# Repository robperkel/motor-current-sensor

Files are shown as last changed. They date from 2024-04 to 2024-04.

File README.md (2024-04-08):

# Hall Effect Current Sensor

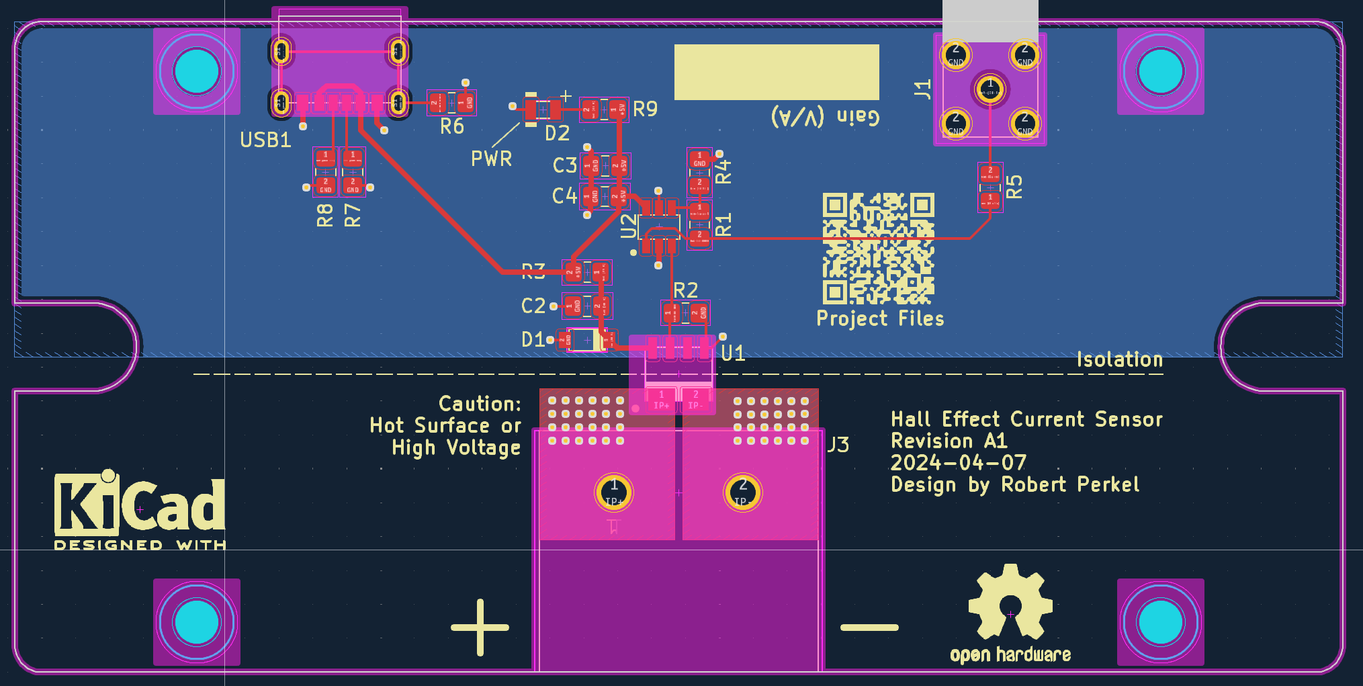
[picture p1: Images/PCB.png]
PCB Screenshot
  

## Disclaimer

**Build and use this circuit at your own risk.** This circuit has not been tested to determine the maximum current possible (without the PCB igniting/melting) or the maximum input voltage on the current sensing side.

If high voltages are applied to the current sense side, the PCB may become a shock hazard. While the current sense side is isolated from the outputs - arcing, debris/dirt, assembly errors or design defects could cause it to jump to the output side. **Excerise extreme caution when working with hazardous voltages.**

## Tools and Components

- [KiCad 8.0.1](https://www.kicad.org/)  
- [FreeCad](https://www.freecad.org/)  

## Measuring the Current

The objective of this circuit is to measure current in an isolated fashion. For me (the author), this is to characterize current flow in a Stepper Motor, however this design can be used in other applications. To perform this task, a [Hall Effect sensor (ACS37030) by Allegro Microsystems](https://www.allegromicro.com/en/products/sense/current-sensor-ics/zero-to-fifty-amp-integrated-conductor-sensor-ics/acs37030-2) is used. 

**Note**: The ACS37030 has multiple different current ranges available, but at the time of this readme, only the 40A part is available. 

**Caution: While the sensor can measure high currents (20A/40A/65A), the PCB is NOT tested or characterized for this.** Use of high copper weight PCB material is likely required.  

This part was choosen due to it's high BW range (DC to 5 MHz), which is uncommon for these ICs. Since the current-side circuit is isolated, it is possible to measure current with high common voltages on the current sense side.

## Driving the Cable

To drive the cable to the oscilloscope, an [MCP633 Operational Amplifier by Microchip](https://www.microchip.com/en-us/product/MCP633) is implemented as a non-inverting amplifier with a gain of 3. The MCP633 has a Gain Bandwidth Product (GBWP) of 24 MHz, which provides enough BW to run at a gain of 3 without limiting the circuit performance. In this configuration, the output of this circuit is 99 mV/A. 

**Note**: The gain of the circuit can be changed by modifying the ratio of R1/R4 in the schematic. 

Power for this board is supplied over USB-C (at 5V). The ACS37030 is designed for 3V operation, so a simple Zener shunt regulator is used to regulate the power supply for the sensor, while the operational amplifier uses the raw USB bus voltage.

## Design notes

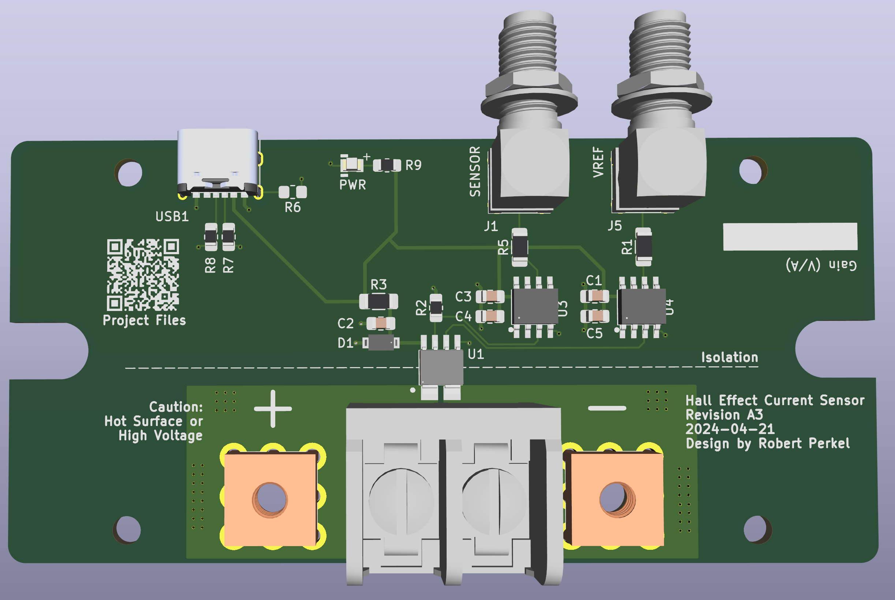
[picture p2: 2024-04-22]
Images/3D PCB Render.png

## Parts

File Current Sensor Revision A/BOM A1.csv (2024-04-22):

Reference | Value | Footprint | Qty | DNP
C1,C2,C3 | 0.1uF | Capacitor_SMD:C_0805_2012Metric_Pad1.18x1.45mm_HandSolder | 3
C4 | 10uF | Capacitor_SMD:C_0805_2012Metric_Pad1.18x1.45mm_HandSolder | 1
C5 | 10uF | Capacitor_SMD:C_0805_2012Metric_Pad1.18x1.45mm_HandSolder | 1 | DNP
D1 | MMSZ4684T1G | StandardPackages_Custom:SOT-123 | 1
D2 | LED | StandardPackages_Custom:LED 0805 | 1
J1,J5 | SMA | Current Sensor PCB Library:CONSMA002-L-G | 2
J2,J4 | 74650094R | Current Sensor PCB Library:74650094R | 2
J3 | Screw_Terminal_01x02 | Current Sensor PCB Library:6PCV-02-007 | 1
R1,R3,R5 | 50 | Resistor_SMD:R_1206_3216Metric_Pad1.30x1.75mm_HandSolder | 3
R2 | 100k | Resistor_SMD:R_0805_2012Metric_Pad1.20x1.40mm_HandSolder | 1
R6 | 0 | Resistor_SMD:R_0805_2012Metric_Pad1.20x1.40mm_HandSolder | 1 | DNP
R7,R8 | 5.1k | Resistor_SMD:R_0805_2012Metric_Pad1.20x1.40mm_HandSolder | 2
R9 | 1.8k | Resistor_SMD:R_0805_2012Metric_Pad1.20x1.40mm_HandSolder | 1
U1 | ACS37030 | Current Sensor PCB Library:Custom 6-pin SOIC (only for ACS37030ACS37032) | 1
U3,U4 | MCP631 | StandardPackages_Custom:SOIC-8 | 2
USB1 | USB_C_Receptacle_PowerOnly_6P | Current Sensor PCB Library:10164359-00011LF | 1

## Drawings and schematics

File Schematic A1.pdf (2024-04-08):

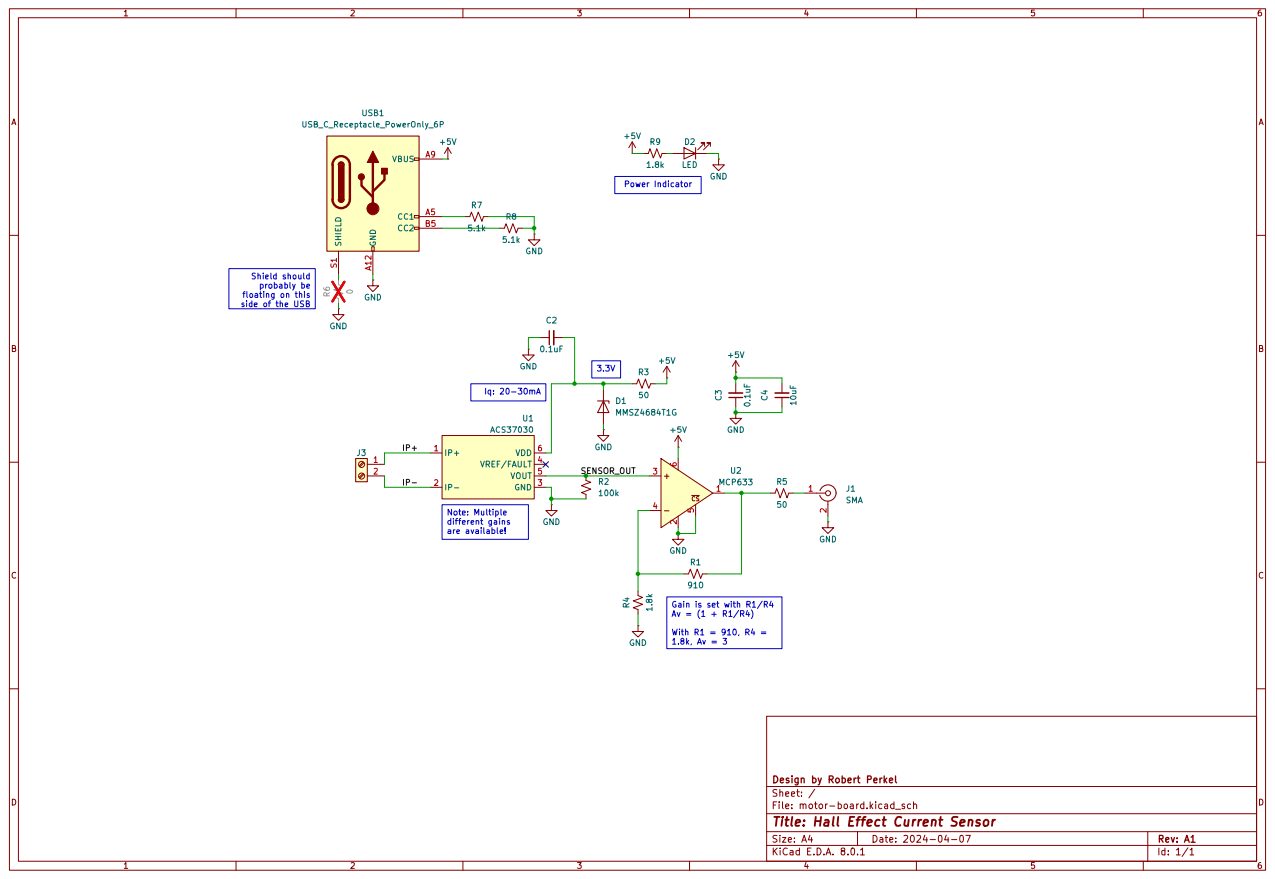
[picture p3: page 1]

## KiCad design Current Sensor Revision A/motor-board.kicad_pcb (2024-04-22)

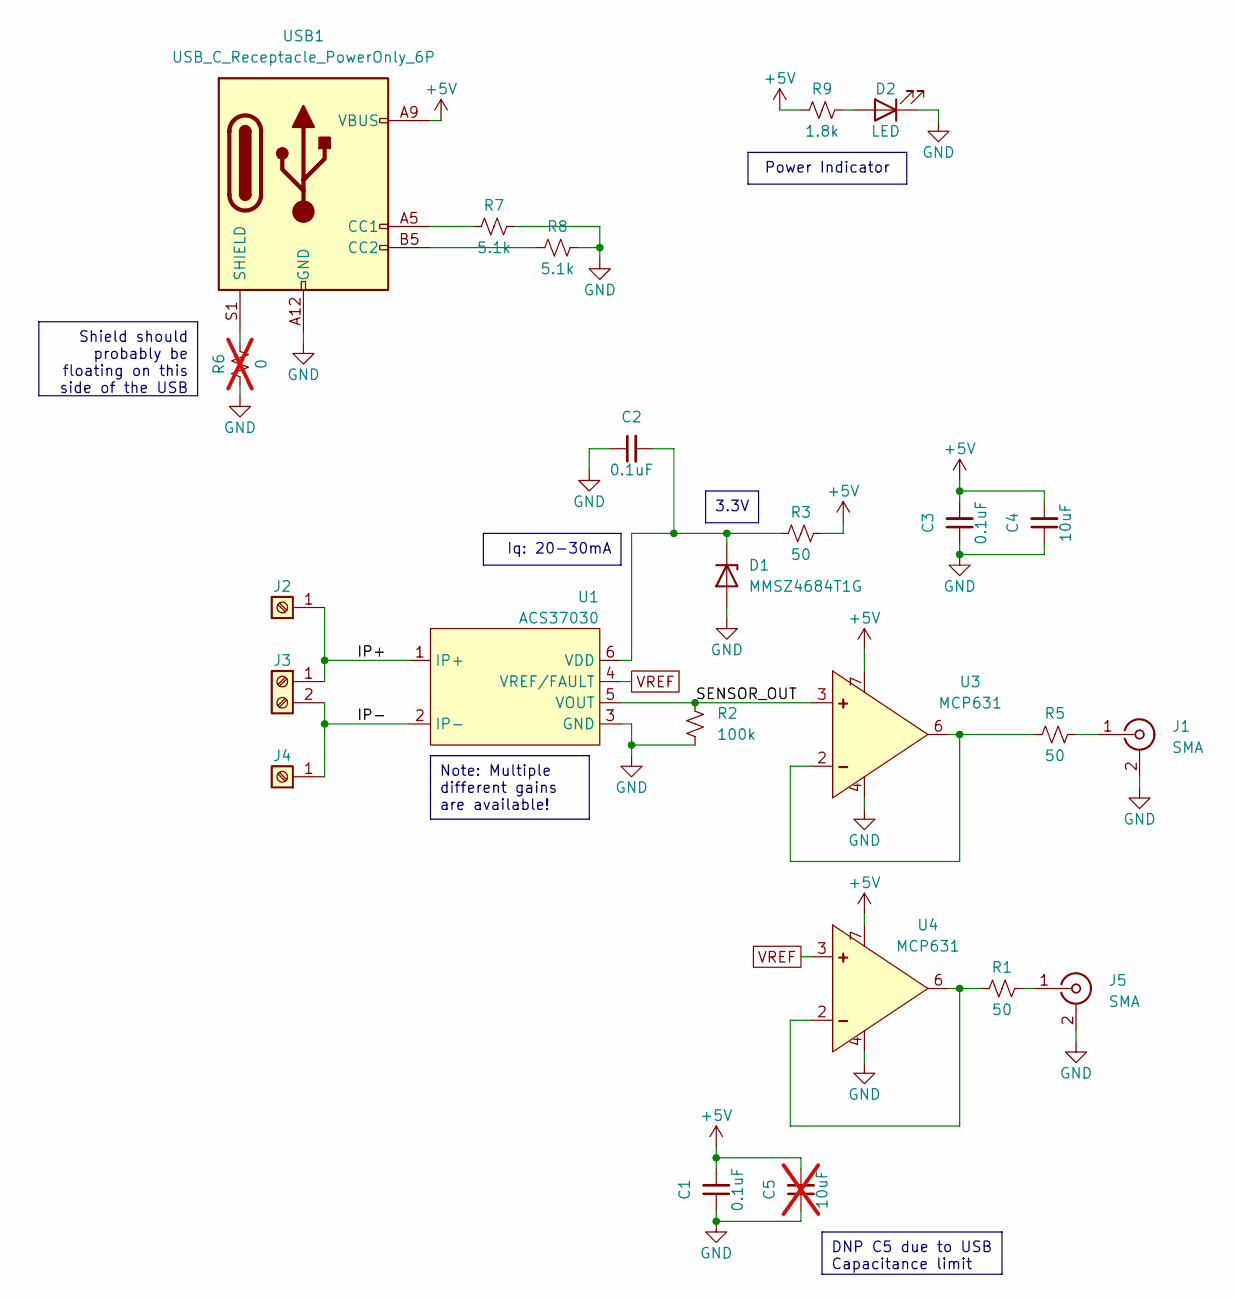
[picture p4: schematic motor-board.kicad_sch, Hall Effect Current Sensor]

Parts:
C1, C2, C3: 0.1uF; C_0805_2012Metric_Pad1.18x1.45mm_HandSolder
C4: 10uF; C_0805_2012Metric_Pad1.18x1.45mm_HandSolder
C5: 10uF; C_0805_2012Metric_Pad1.18x1.45mm_HandSolder; not fitted
D1: MMSZ4684T1G; SOT-123
D2: LED; LED 0805
J1, J5: SMA; CONSMA002-L-G
J2, J4: 74650094R
J3: Screw_Terminal_01x02; 6PCV-02-007
R1, R3, R5: 50; R_1206_3216Metric_Pad1.30x1.75mm_HandSolder
R2: 100k; R_0805_2012Metric_Pad1.20x1.40mm_HandSolder
R6: 0; R_0805_2012Metric_Pad1.20x1.40mm_HandSolder; not fitted
R7, R8: 5.1k; R_0805_2012Metric_Pad1.20x1.40mm_HandSolder
R9: 1.8k; R_0805_2012Metric_Pad1.20x1.40mm_HandSolder
U1: ACS37030; Custom 6-pin SOIC (only for ACS37030ACS37032)
U3, U4: MCP631; SOIC-8
USB1: USB_C_Receptacle_PowerOnly_6P; 10164359-00011LF

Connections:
+5V: C1.2, C3.2, C4.2, C5.2, R3.2, R9.1, U3.7 (VDD), U4.7 (VDD), USB1.A9 (VBUS), USB1.B9 (VBUS)
/IP+: J2.1, J3.1, U1.1 (IP+)
/IP-: J3.2, J4.1, U1.2 (IP-)
/SENSOR_OUT: R2.1, U1.5 (VOUT), U3.3 (IN+)
GND: C1.1, C2.1, C3.1, C4.1, C5.1, D1.2 (A), D2.1 (K), J1.2 (Ext), J5.2 (Ext), R2.2, R6.1, R7.2, R8.2, U1.3 (GND), U3.4 (VSS), U4.4 (VSS), USB1.A12 (GND), USB1.B12 (GND)
unnamed: C2.2, D1.1 (K), R3.1, U1.6 (VDD)
unnamed: D2.2 (A), R9.2
unnamed: J1.1 (In), R5.2
unnamed: J5.1 (In), R1.2
unnamed: R5.1, U3.2 (IN-), U3.6 (VOUT)
unnamed: R1.1, U4.2 (IN-), U4.6 (VOUT)
unnamed: R7.1, USB1.A5 (CC1)
unnamed: R8.1, USB1.B5 (CC2)
unnamed: R6.2, USB1.S1 (SHIELD)
VREF: U1.4 (VREF/FAULT), U4.3 (IN+)

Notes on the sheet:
Power Indicator
DNP C5 due to USB Capacitance limit
3.3V
Note: Multiple different gains are available!
Iq: 20-30mA
Shield should probably be floating on this side of the USB

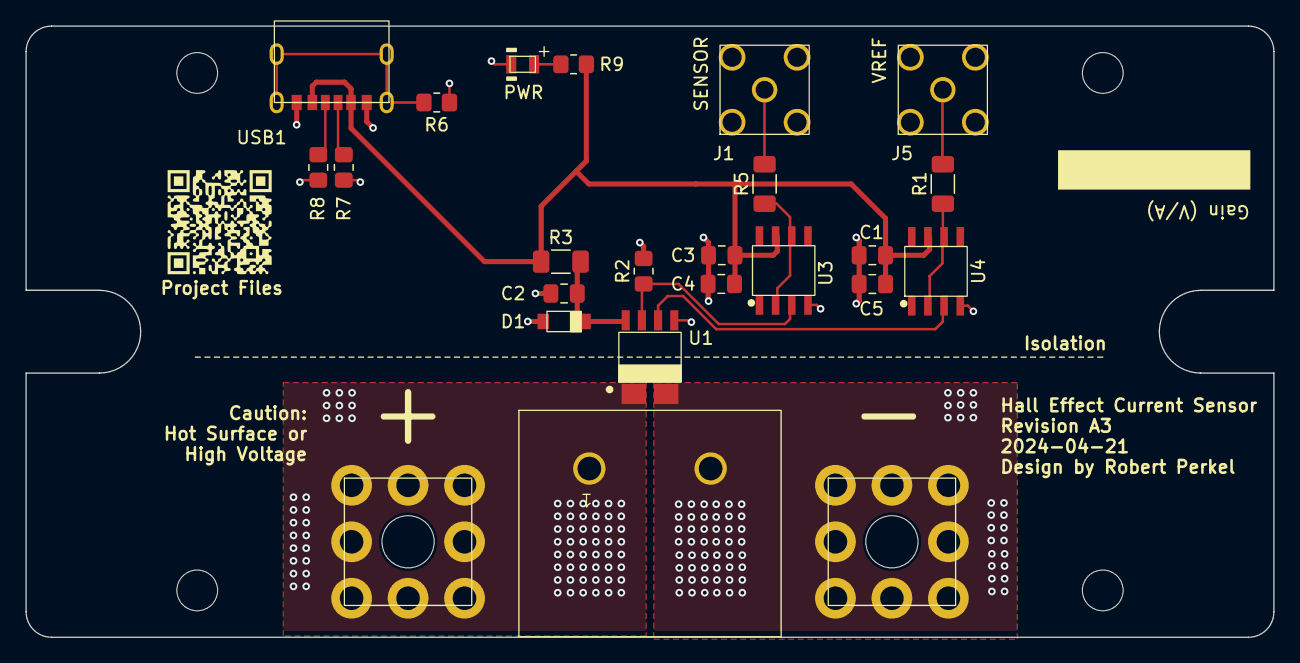
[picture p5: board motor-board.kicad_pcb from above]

Board: 2 copper layers, 98.0 x 48.0 mm, 24 parts (0 on the bottom side), 15 nets.

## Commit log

2024-04-08 PCB Files
    [motor-board.kicad_pcb, motor-board.kicad_sch]
2024-04-08 Renamed KiCad files to be consistent
    [motor-board.kicad_pcb, motor-board.kicad_sch]
2024-04-22 Added A2/A3 PCB files and 3D Board Render
    [BOM A1.csv, motor-board.kicad_pcb, motor-board.kicad_sch]
